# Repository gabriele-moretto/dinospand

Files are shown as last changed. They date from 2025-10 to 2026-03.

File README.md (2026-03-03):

# DinoSpand

The purpose of this board is to be mounted on a fertilizer spreader (an agricultural tool) to manage the drawer in which we load/unload the fertilizer.
While managing the tool, we'll see all the information in the cabin on the little OLED screen on the board, but also we will able to connect the device to our smartphone in order to managing some settings.

## Hardware

The microcontroller used is an ESP32-s3, which is useful for the right number of GPIO we need and for the bluetooth functions.

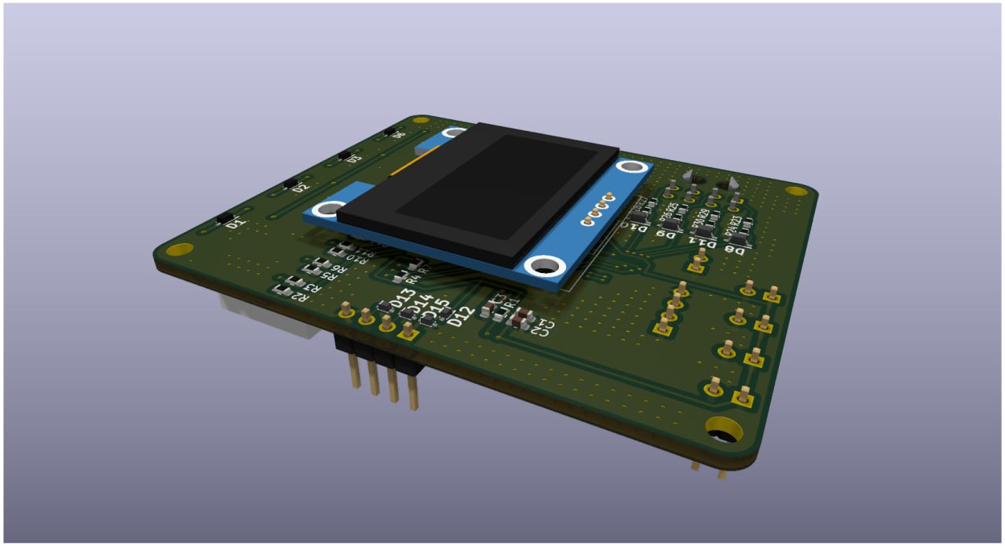
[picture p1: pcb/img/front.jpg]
Front

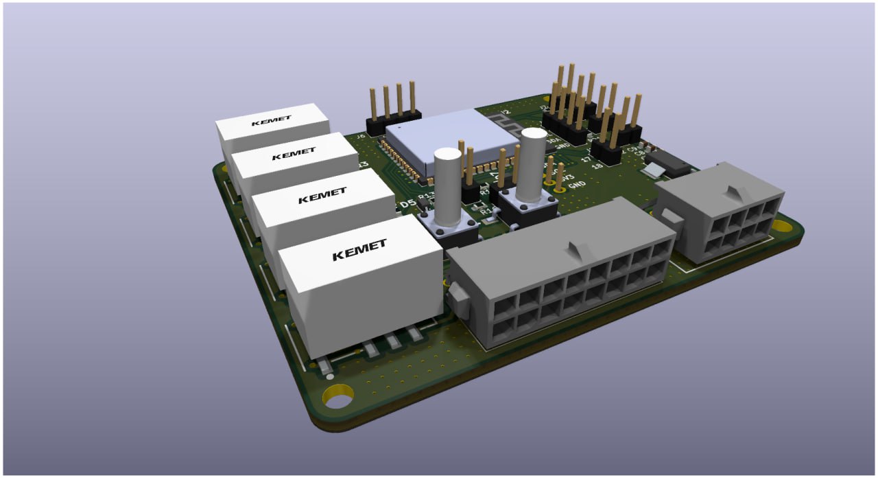
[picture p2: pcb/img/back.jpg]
Back


## Firmware

## [PCBWay](https://www.pcbway.com/) production
I had a great experience working with **PCBWay** through their sponsorship program. They supported my project by manufacturing and shipping a fully assembled PCB, which allowed me to turn my design into a real, working device.

**Key points:**
- PCB manufacturing
- High-quality fabrication and assembly
- Easy ordering process
- Fast production and shipping
- Reliable results

Many thanks to PCBWay for supporting this project!

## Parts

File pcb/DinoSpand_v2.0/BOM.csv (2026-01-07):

Id | Designator | Footprint | Quantity | Designation | Supplier and ref
1 | D7,D5,D4,D11,D8,D10,D9 | SOD2512X110N | 7 | 3.3V
2 | C7,C12,C6,C13,C1 | C_0603_1608Metric | 5 | 10uF
3 | C4,C10,C9 | CP_Radial_D4.0mm_P2.00mm | 3 | xuF
4 | Q2,Q4,Q1,Q3 | SOT96P240X110-3N | 4 | DMN62D0U-7
5 | R21,R16,R22,R8,R19,R20,R18,R12,R1,R6,R11,R29,R4,R15,R3,R25,R7,R27,R23 | R_0603_1608Metric | 19 | 10k
6 | S1,S2 | SW_1571563-6 | 2 | 1571563-6
7 | C8,C11,C5,C14,C15 | C_0603_1608Metric | 5 | xuF
8 | K3,K1,K2,K4 | EE2-5NU | 4 | EE2-5NU
9 | U3,U4 | SOT230P700X180-4N | 2 | LT1963AEST-3.3#TRPBF
10 | J11 | 37946198 | 1 | 3-794619-8
11 | R32,R31 | R_0603_1608Metric | 2 | 100
12 | D16 | LED_0603_1608Metric | 1 | LED
13 | D17 | LED_D3.0mm | 1 | LED
14 | U2 | ESP32S3WROOM1N4 | 1 | ESP32-S3-WROOM-1-N4
15 | R9,R13,R17,R30,R26,R24,R28 | R_0603_1608Metric | 7 | 2.8k
16 | J3 | 47946196 | 1 | 4-794619-6
17 | R10,R14,R2,R5 | R_0603_1608Metric | 4 | 10
18 | D15,D14,D13 | SODFL1608X70N | 3 | SZESD5B5.0ST5G
19 | C2 | C_0603_1608Metric | 1 | 0.1uF
20 | D6,D3,D1,D2 | SODFL2512X90N | 4 | D
21 | C3 | C_0603_1608Metric | 1 | 1uF
22 | D12 | SODFL1608X70N | 1 | D
23 | U1 | 128x64OLED | 1 | Oled64x128

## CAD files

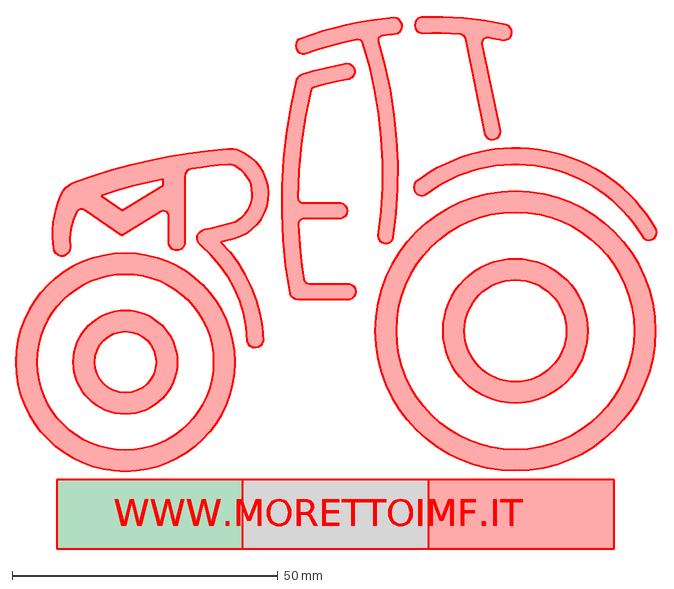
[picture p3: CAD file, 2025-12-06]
logo/logo_MorettoIMF.dxf
WWW.MORETTOIMF.IT

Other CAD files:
logo/Logo Moretto-rev-31-08-2021.dwg

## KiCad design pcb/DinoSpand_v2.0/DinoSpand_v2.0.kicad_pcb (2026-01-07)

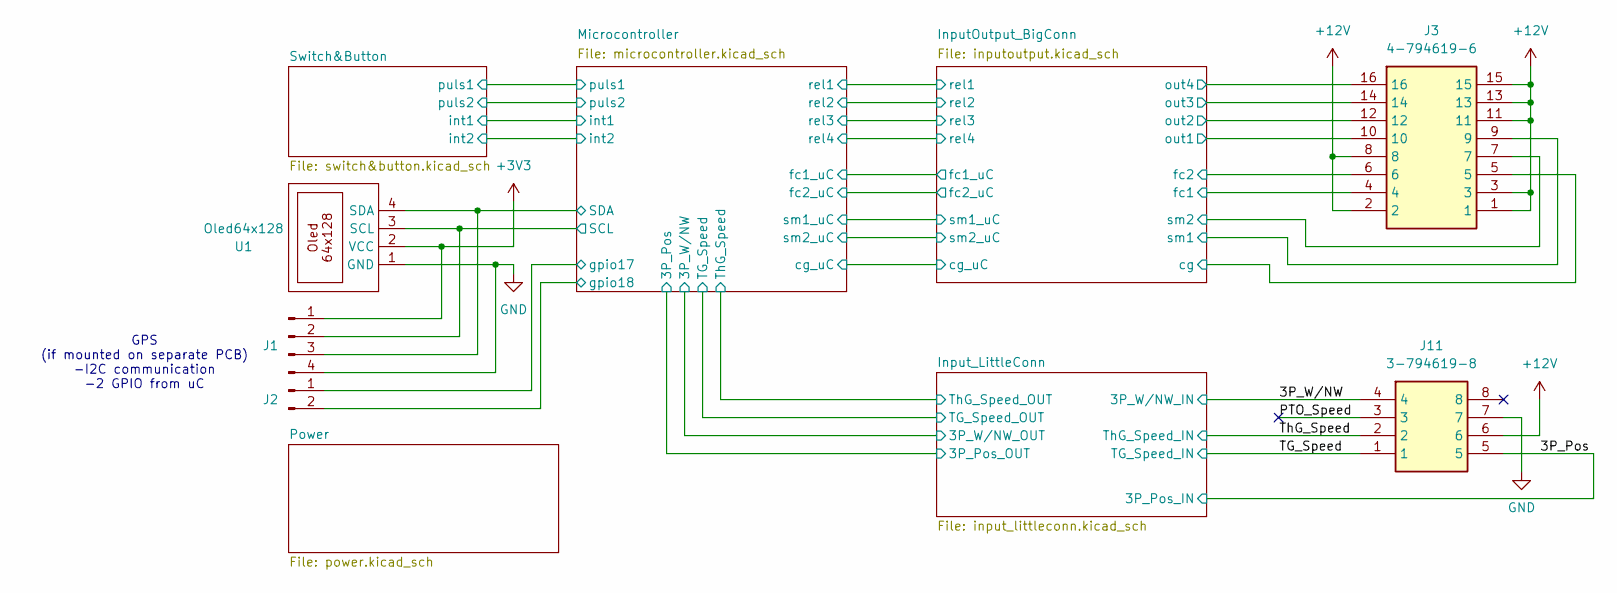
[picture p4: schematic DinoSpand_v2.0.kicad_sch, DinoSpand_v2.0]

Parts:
J1: Conn_01x04_Pin; PinHeader_1x04_P2.54mm_Vertical
J2: Conn_01x02_Pin; PinHeader_1x02_P2.54mm_Vertical
J3: 4-794619-6; 47946196; Mouser Part Number 571-4-794619-6
J11: 3-794619-8; 37946198; Mouser Part Number 571-3-794619-8
U1: Oled64x128; 128x64OLED

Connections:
+3V3: J1.1, U1.2 (VCC); also elsewhere on the board
+12V: J3.1, J3.2, J3.3, J3.8, J3.11, J3.13, J3.15, J11.6; also elsewhere on the board
/3P_Pos: J11.5; also elsewhere on the board
/3P_W/NW: J11.4; also elsewhere on the board
/InputOutput_BigConn/cg: J3.5; also elsewhere on the board
/InputOutput_BigConn/out1: J3.10; also elsewhere on the board
/InputOutput_BigConn/out2: J3.12; also elsewhere on the board
/InputOutput_BigConn/out3: J3.14; also elsewhere on the board
/InputOutput_BigConn/out4: J3.16; also elsewhere on the board
/InputOutput_BigConn/sm1: J3.9; also elsewhere on the board
/InputOutput_BigConn/sm2: J3.7; also elsewhere on the board
/Microcontroller/GPIO10: J3.4; also elsewhere on the board
/Microcontroller/GPIO11: J3.6; also elsewhere on the board
/Microcontroller/GPIO15: J1.3, U1.4 (SDA); also elsewhere on the board
/Microcontroller/GPIO16: J1.2, U1.3 (SCL); also elsewhere on the board
/Microcontroller/GPIO17: J2.1; also elsewhere on the board
/Microcontroller/GPIO18: J2.2; also elsewhere on the board
/PTO_Speed: J11.3
/TG_Speed: J11.1; also elsewhere on the board
/ThG_Speed: J11.2; also elsewhere on the board
GND: J1.4, J11.7, U1.1 (GND); also elsewhere on the board

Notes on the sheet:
GPS (if mounted on separate PCB) -I2C communication -2 GPIO from uC

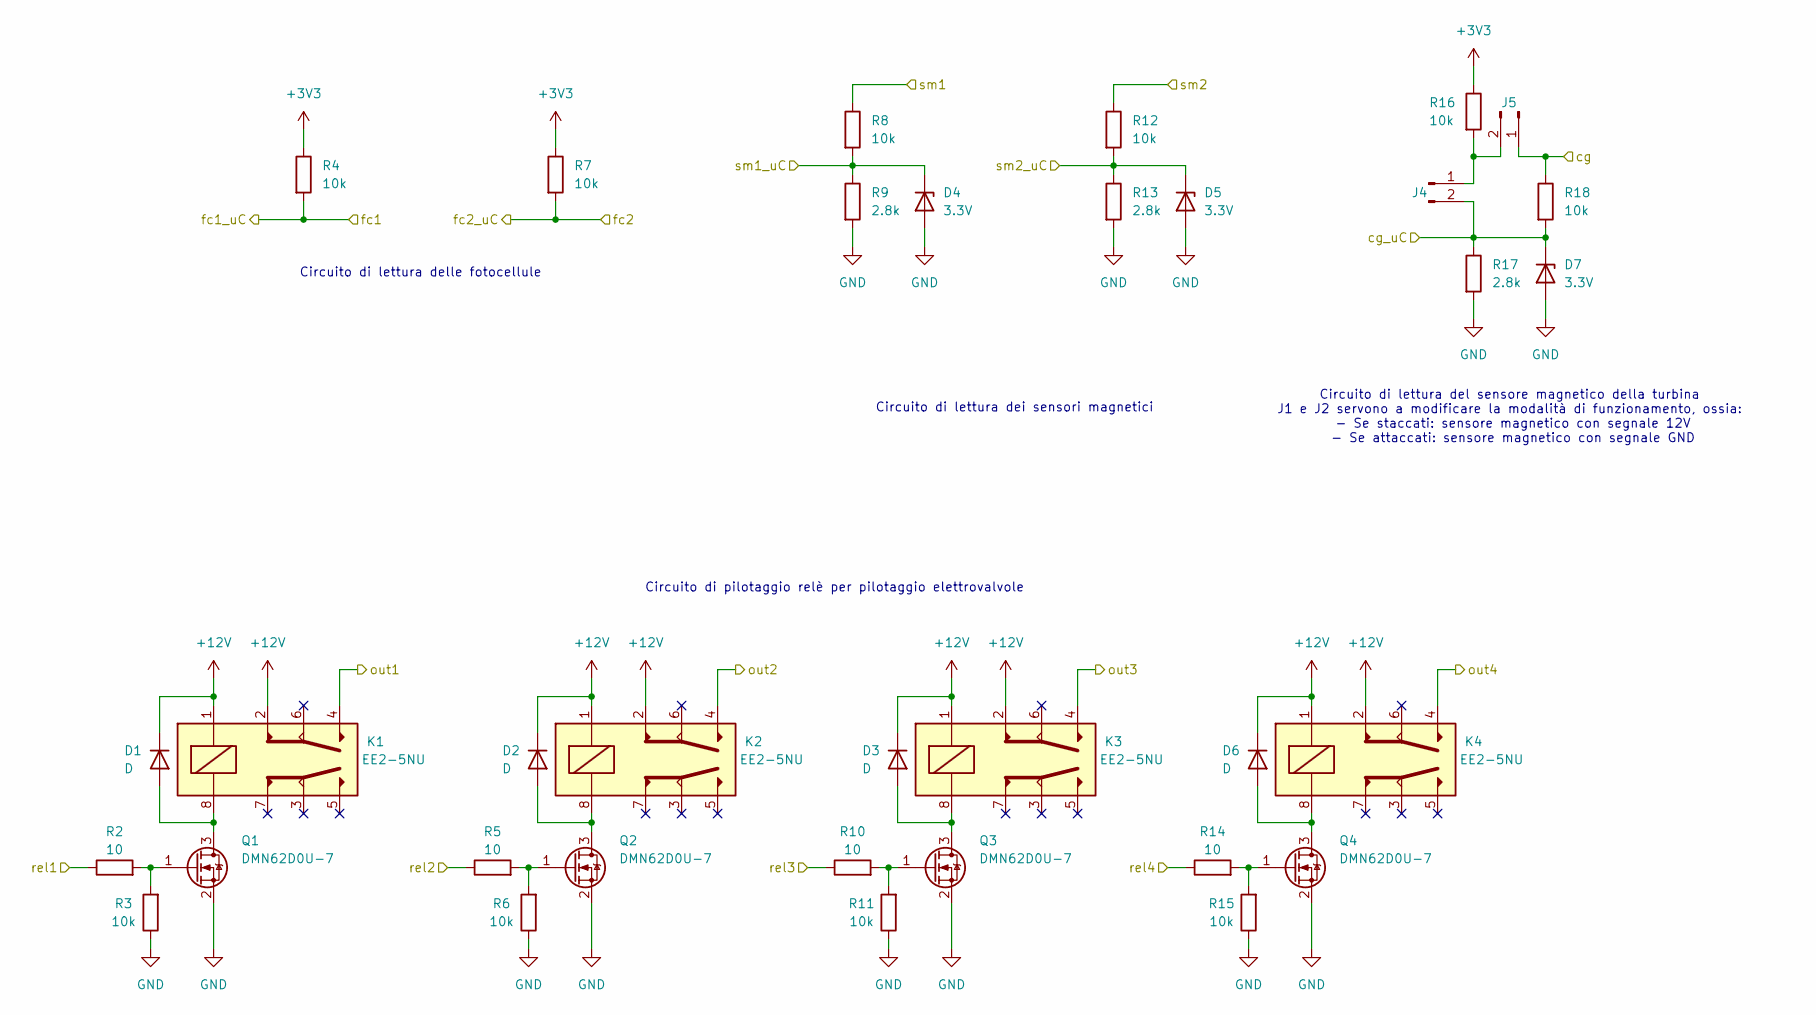
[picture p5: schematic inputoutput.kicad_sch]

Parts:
D1, D2, D3, D6: D; SODFL2512X90N
D4, D5, D7: 3.3V; SOD2512X110N
J4, J5: Conn_01x02_Pin; PinHeader_1x02_P2.54mm_Vertical
K1, K2, K3, K4: EE2-5NU; Mouser Part Number 80-EE2-5NU
Q1, Q2, Q3, Q4: DMN62D0U-7; SOT96P240X110-3N; Mouser Part Number 621-DMN62D0U-7
R2, R5, R10, R14: 10; R_0603_1608Metric
R3, R4, R6, R7, R8, R11, R12, R15, R16, R18: 10k; R_0603_1608Metric
R9, R13, R17: 2.8k; R_0603_1608Metric

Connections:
+3V3: R4.1, R7.1, R16.1; also elsewhere on the board
+12V: D1.1 (K), D2.1 (K), D3.1 (K), D6.1 (K), K1.1, K1.2, K2.1, K2.2, K3.1, K3.2, K4.1, K4.2; also elsewhere on the board
/InputOutput_BigConn/cg: J5.1, R18.1; also elsewhere on the board
/InputOutput_BigConn/out1: K1.4; also elsewhere on the board
/InputOutput_BigConn/out2: K2.4; also elsewhere on the board
/InputOutput_BigConn/out3: K3.4; also elsewhere on the board
/InputOutput_BigConn/out4: K4.4; also elsewhere on the board
/InputOutput_BigConn/sm1: R8.1; also elsewhere on the board
/InputOutput_BigConn/sm2: R12.1; also elsewhere on the board
/Microcontroller/GPIO10: R4.2; also elsewhere on the board
/Microcontroller/GPIO11: R7.2; also elsewhere on the board
/Microcontroller/GPIO12: D4.1 (K), R8.2, R9.1; also elsewhere on the board
/Microcontroller/GPIO13: D5.1 (K), R12.2, R13.1; also elsewhere on the board
/Microcontroller/GPIO14: D7.1 (K), J4.2, R17.1, R18.2; also elsewhere on the board
/Microcontroller/GPIO21: R2.1; also elsewhere on the board
/Microcontroller/GPIO37: R14.1; also elsewhere on the board
/Microcontroller/GPIO47: R5.1; also elsewhere on the board
/Microcontroller/GPIO48: R10.1; also elsewhere on the board
GND: D4.2 (A), D5.2 (A), D7.2 (A), Q1.2 (S), Q2.2 (S), Q3.2 (S), Q4.2 (S), R3.1, R6.1, R9.2, R11.1, R13.2, R15.1, R17.2; also elsewhere on the board
unnamed: D1.2 (A), K1.8, Q1.3 (D)
unnamed: D2.2 (A), K2.8, Q2.3 (D)
unnamed: D3.2 (A), K3.8, Q3.3 (D)
unnamed: D6.2 (A), K4.8, Q4.3 (D)
unnamed: J4.1, J5.2, R16.2
unnamed: Q1.1 (G), R2.2, R3.2
unnamed: Q2.1 (G), R5.2, R6.2
unnamed: Q3.1 (G), R10.2, R11.2
unnamed: Q4.1 (G), R14.2, R15.2

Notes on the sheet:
Circuito di pilotaggio relè per pilotaggio elettrovalvole
Circuito di lettura del sensore magnetico della turbina J1 e J2 servono a modificare la modalità di funzionamento, ossia: - Se staccati: sensore magnetico con segnale 12V - Se attaccati: sensore magnetico con segnale GND
Circuito di lettura dei sensori magnetici
Circuito di lettura delle fotocellule

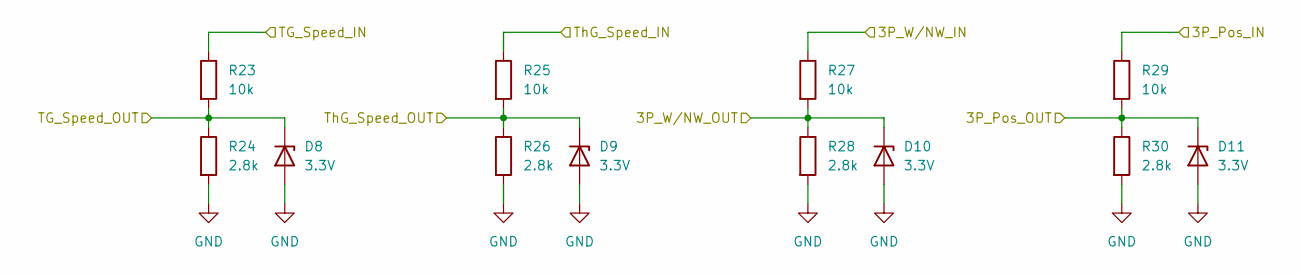
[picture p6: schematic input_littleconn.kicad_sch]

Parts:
D8, D9, D10, D11: 3.3V; SOD2512X110N
R23, R25, R27, R29: 10k; R_0603_1608Metric
R24, R26, R28, R30: 2.8k; R_0603_1608Metric

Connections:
/3P_Pos: R29.1; also elsewhere on the board
/3P_W/NW: R27.1; also elsewhere on the board
/Microcontroller/GPIO9: D10.1 (K), R27.2, R28.1; also elsewhere on the board
/Microcontroller/GPIO35: D9.1 (K), R25.2, R26.1; also elsewhere on the board
/Microcontroller/GPIO36: D8.1 (K), R23.2, R24.1; also elsewhere on the board
/Microcontroller/GPIO38: D11.1 (K), R29.2, R30.1; also elsewhere on the board
/TG_Speed: R23.1; also elsewhere on the board
/ThG_Speed: R25.1; also elsewhere on the board
GND: D8.2 (A), D9.2 (A), D10.2 (A), D11.2 (A), R24.2, R26.2, R28.2, R30.2; also elsewhere on the board

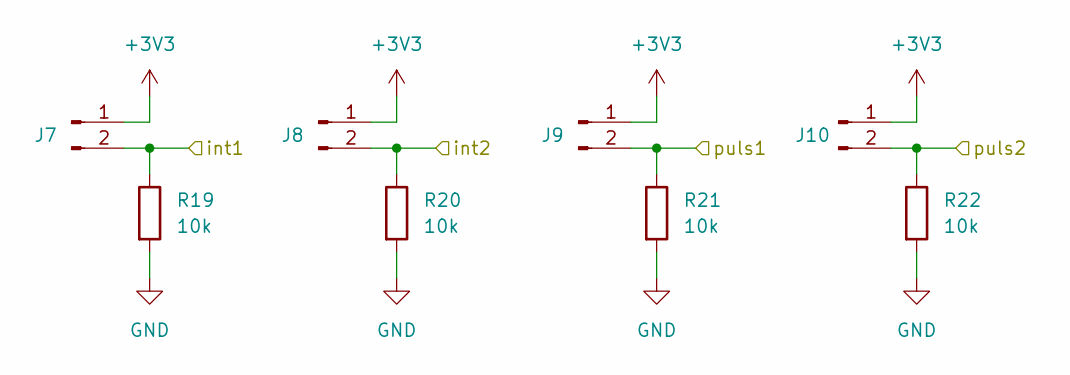
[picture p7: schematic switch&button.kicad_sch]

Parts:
J7, J8, J9, J10: Conn_01x02_Pin; PinHeader_1x02_P2.54mm_Vertical
R19, R20, R21, R22: 10k; R_0603_1608Metric

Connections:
+3V3: J7.1, J8.1, J9.1, J10.1; also elsewhere on the board
/Microcontroller/GPIO4: J7.2, R19.1; also elsewhere on the board
/Microcontroller/GPIO5: J8.2, R20.1; also elsewhere on the board
/Microcontroller/GPIO6: J9.2, R21.1; also elsewhere on the board
/Microcontroller/GPIO7: J10.2, R22.1; also elsewhere on the board
GND: R19.2, R20.2, R21.2, R22.2; also elsewhere on the board

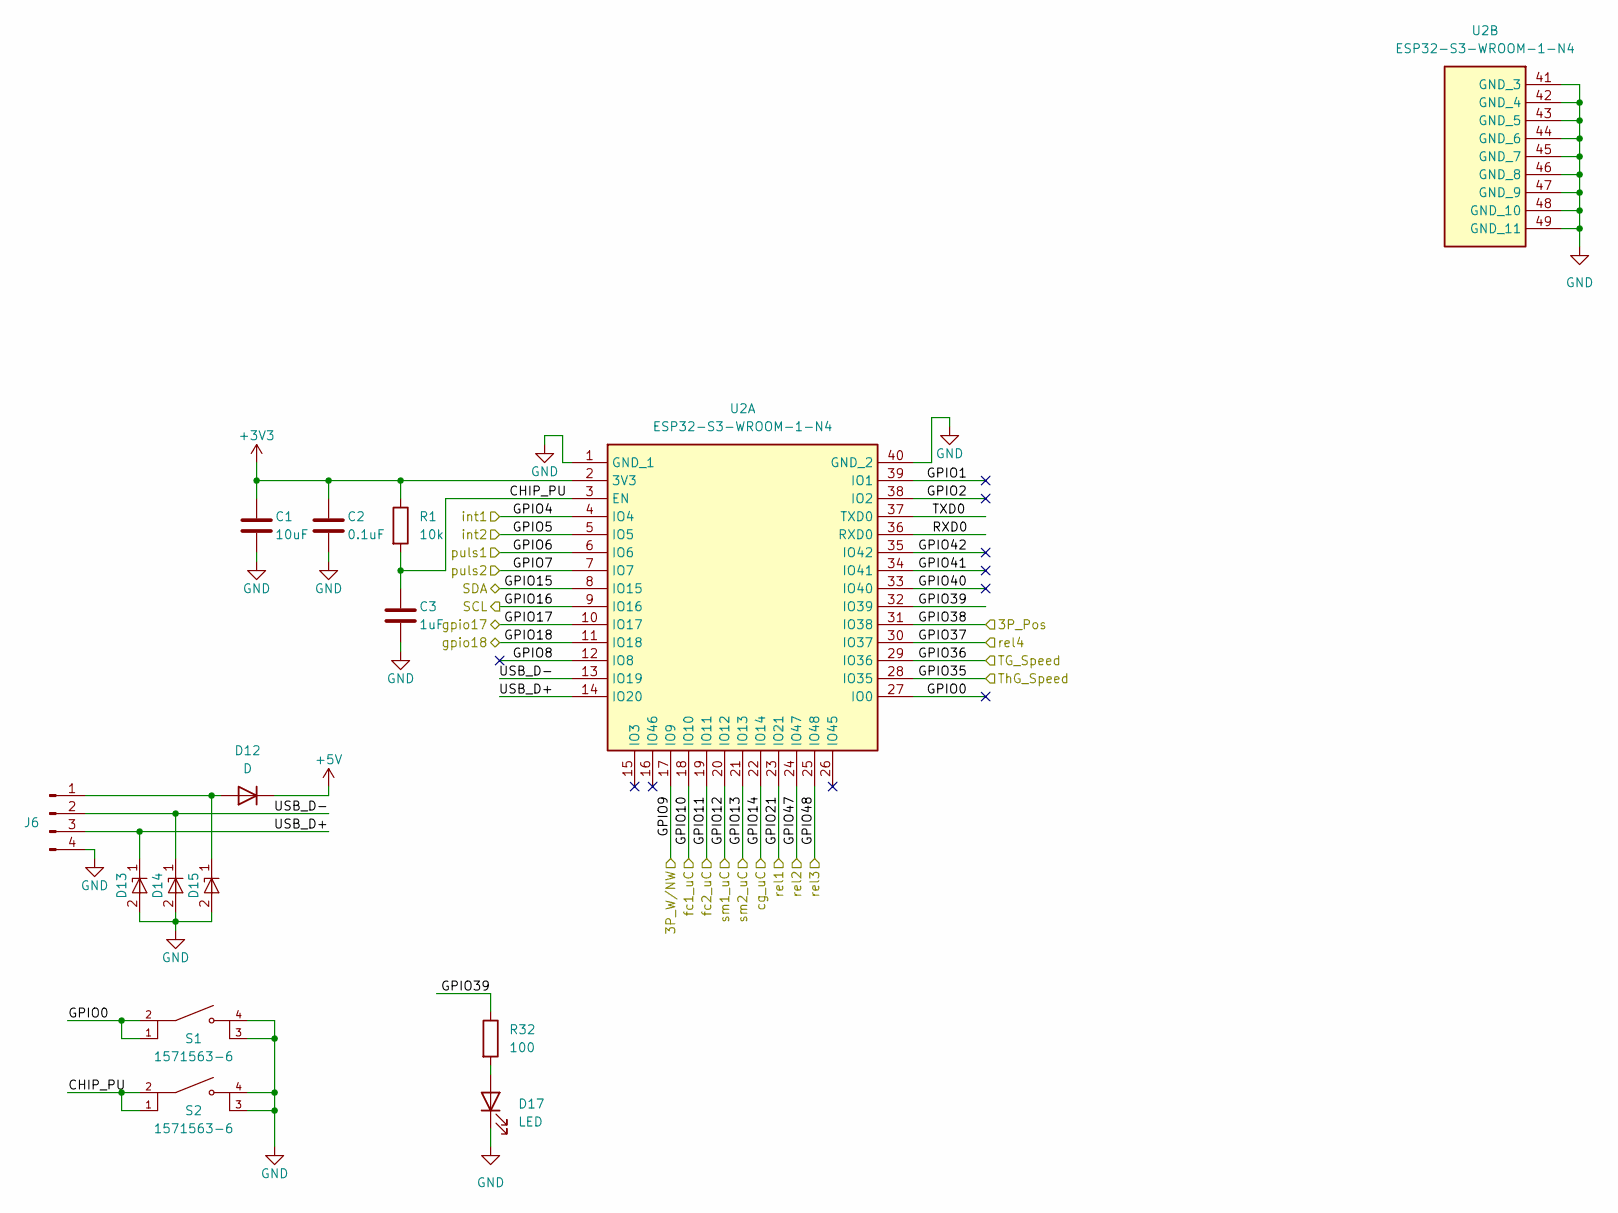
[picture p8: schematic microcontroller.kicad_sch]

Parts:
C1: 10uF; C_0603_1608Metric
C2: 0.1uF; C_0603_1608Metric
C3: 1uF; C_0603_1608Metric
D12: D; SODFL1608X70N
D13, D14, D15: SZESD5B5.0ST5G; SODFL1608X70N; Mouser Part Number 863-SZESD5B5.0ST5G
D17: LED; LED_D3.0mm
J6: Conn_01x04_Pin; PinHeader_1x04_P2.54mm_Vertical
R1: 10k; R_0603_1608Metric
R32: 100; R_0603_1608Metric
S1, S2: 1571563-6; SW_1571563-6; PARTREV V
U2: ESP32-S3-WROOM-1-N4; ESP32S3WROOM1N4; Mouser Part Number 356-ESP32-S3WROOM1N4

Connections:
+3V3: C1.1, C2.1, R1.1, U2.2 (3V3); also elsewhere on the board
+5V: D12.1 (K); also elsewhere on the board
/Microcontroller/CHIP_PU: C3.1, R1.2, S2.1, S2.2, U2.3 (EN)
/Microcontroller/GPIO0: S1.1, S1.2, U2.27 (IO0)
/Microcontroller/GPIO1: U2.39 (IO1)
/Microcontroller/GPIO2: U2.38 (IO2)
/Microcontroller/GPIO4: U2.4 (IO4); also elsewhere on the board
/Microcontroller/GPIO5: U2.5 (IO5); also elsewhere on the board
/Microcontroller/GPIO6: U2.6 (IO6); also elsewhere on the board
/Microcontroller/GPIO7: U2.7 (IO7); also elsewhere on the board
/Microcontroller/GPIO8: U2.12 (IO8)
/Microcontroller/GPIO9: U2.17 (IO9); also elsewhere on the board
/Microcontroller/GPIO10: U2.18 (IO10); also elsewhere on the board
/Microcontroller/GPIO11: U2.19 (IO11); also elsewhere on the board
/Microcontroller/GPIO12: U2.20 (IO12); also elsewhere on the board
/Microcontroller/GPIO13: U2.21 (IO13); also elsewhere on the board
/Microcontroller/GPIO14: U2.22 (IO14); also elsewhere on the board
/Microcontroller/GPIO15: U2.8 (IO15); also elsewhere on the board
/Microcontroller/GPIO16: U2.9 (IO16); also elsewhere on the board
/Microcontroller/GPIO17: U2.10 (IO17); also elsewhere on the board
/Microcontroller/GPIO18: U2.11 (IO18); also elsewhere on the board
/Microcontroller/GPIO21: U2.23 (IO21); also elsewhere on the board
/Microcontroller/GPIO35: U2.28 (IO35); also elsewhere on the board
/Microcontroller/GPIO36: U2.29 (IO36); also elsewhere on the board
/Microcontroller/GPIO37: U2.30 (IO37); also elsewhere on the board
/Microcontroller/GPIO38: U2.31 (IO38); also elsewhere on the board
/Microcontroller/GPIO39: R32.1, U2.32 (IO39)
/Microcontroller/GPIO40: U2.33 (IO40)
/Microcontroller/GPIO41: U2.34 (IO41)
/Microcontroller/GPIO42: U2.35 (IO42)
/Microcontroller/GPIO47: U2.24 (IO47); also elsewhere on the board
/Microcontroller/GPIO48: U2.25 (IO48); also elsewhere on the board
/Microcontroller/RXD0: U2.36 (RXD0)
/Microcontroller/TXD0: U2.37 (TXD0)
/Microcontroller/USB_D+: D13.1 (K1), J6.3, U2.14 (IO20)
/Microcontroller/USB_D-: D14.1 (K1), J6.2, U2.13 (IO19)
GND: C1.2, C2.2, C3.2, D13.2 (A), D14.2 (A), D15.2 (A), D17.1 (K), J6.4, S1.3, S1.4, S2.3, S2.4, U2.1 (GND_1), U2.40 (GND_2), U2.41 (GND_3), U2.42 (GND_4), U2.43 (GND_5), U2.44 (GND_6), U2.45 (GND_7), U2.46 (GND_8), U2.47 (GND_9), U2.48 (GND_10), U2.49 (GND_11); also elsewhere on the board
unnamed: D12.2 (A), D15.1 (K1), J6.1
unnamed: D17.2 (A), R32.2

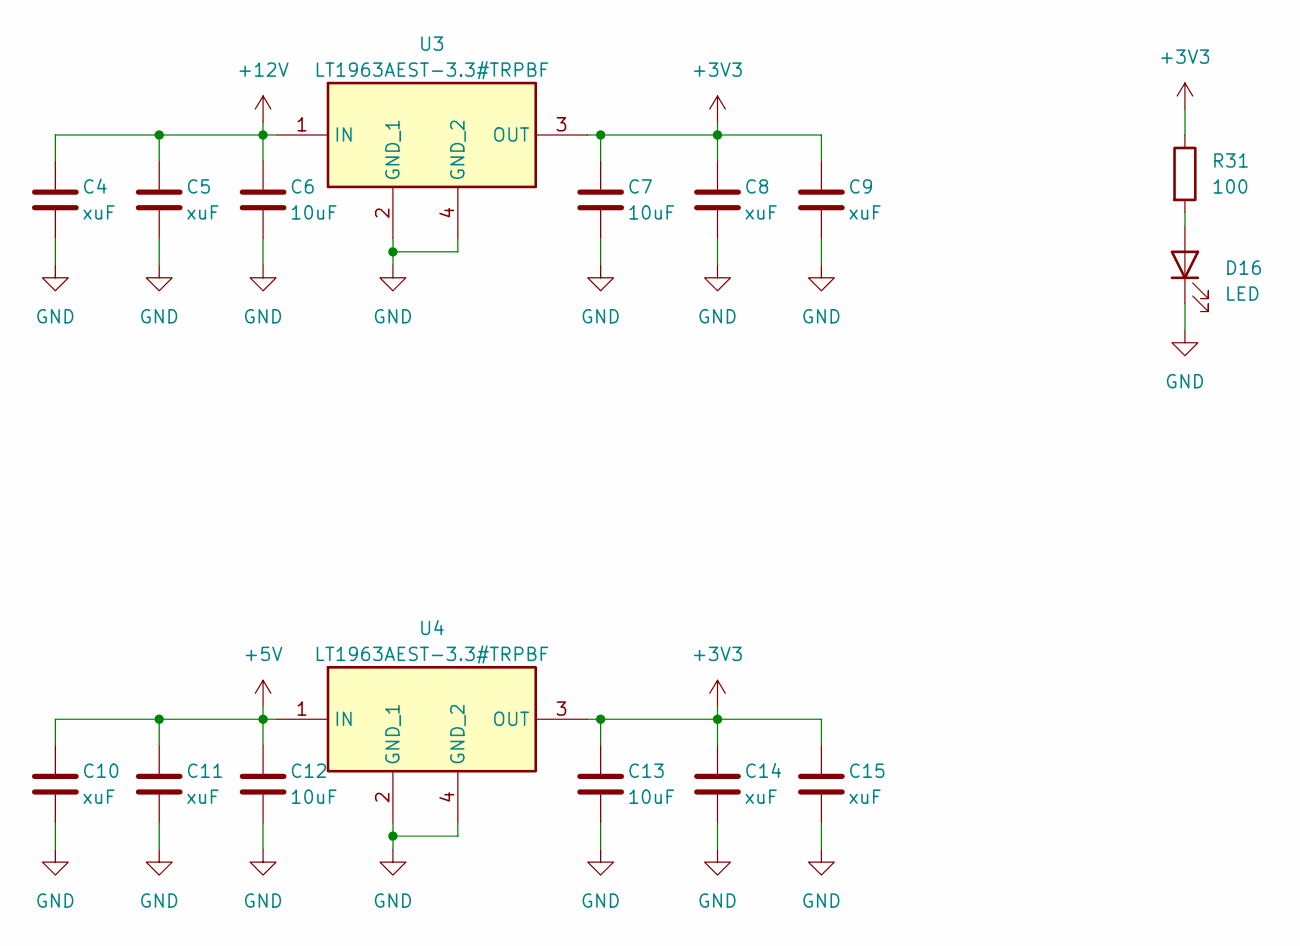
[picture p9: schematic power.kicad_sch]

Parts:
C4, C9, C10: xuF; CP_Radial_D4.0mm_P2.00mm
C5, C8, C11, C14, C15: xuF; C_0603_1608Metric
C6, C7, C12, C13: 10uF; C_0603_1608Metric
D16: LED; LED_0603_1608Metric
R31: 100; R_0603_1608Metric
U3, U4: LT1963AEST-3.3#TRPBF; SOT230P700X180-4N; Mouser Part Number 584-1963AEST-3.3TPF

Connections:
+3V3: C7.1, C8.1, C9.1, C13.1, C14.1, C15.1, R31.1, U3.3 (OUT), U4.3 (OUT); also elsewhere on the board
+5V: C10.1, C11.1, C12.1, U4.1 (IN); also elsewhere on the board
+12V: C4.1, C5.1, C6.1, U3.1 (IN); also elsewhere on the board
GND: C4.2, C5.2, C6.2, C7.2, C8.2, C9.2, C10.2, C11.2, C12.2, C13.2, C14.2, C15.2, D16.1 (K), U3.2 (GND_1), U3.4 (GND_2), U4.2 (GND_1), U4.4 (GND_2); also elsewhere on the board
unnamed: D16.2 (A), R31.2

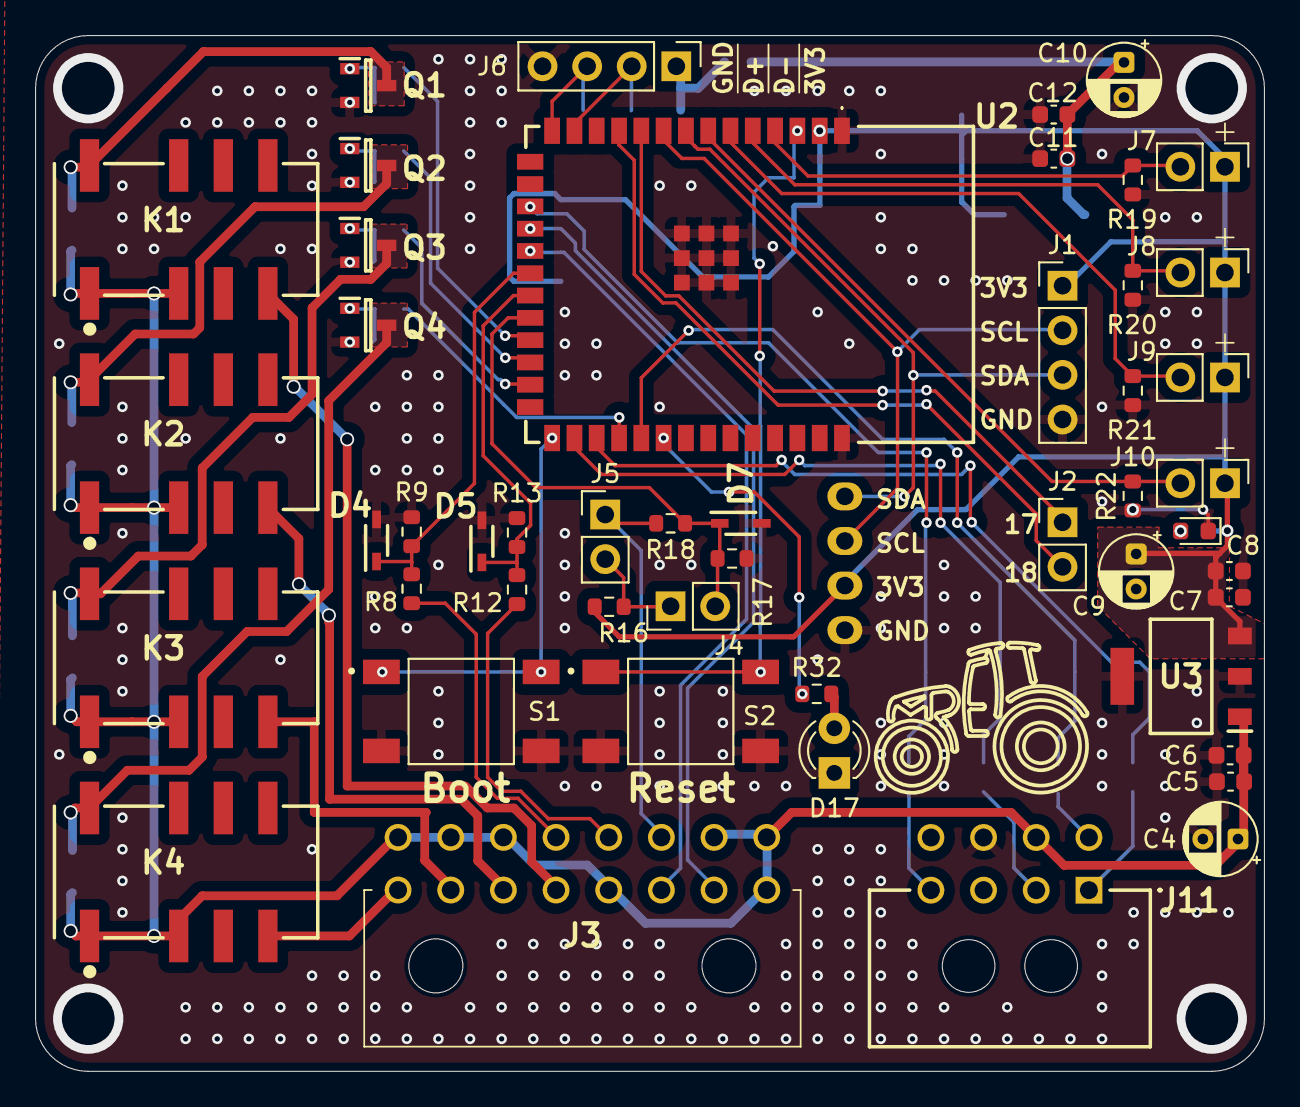
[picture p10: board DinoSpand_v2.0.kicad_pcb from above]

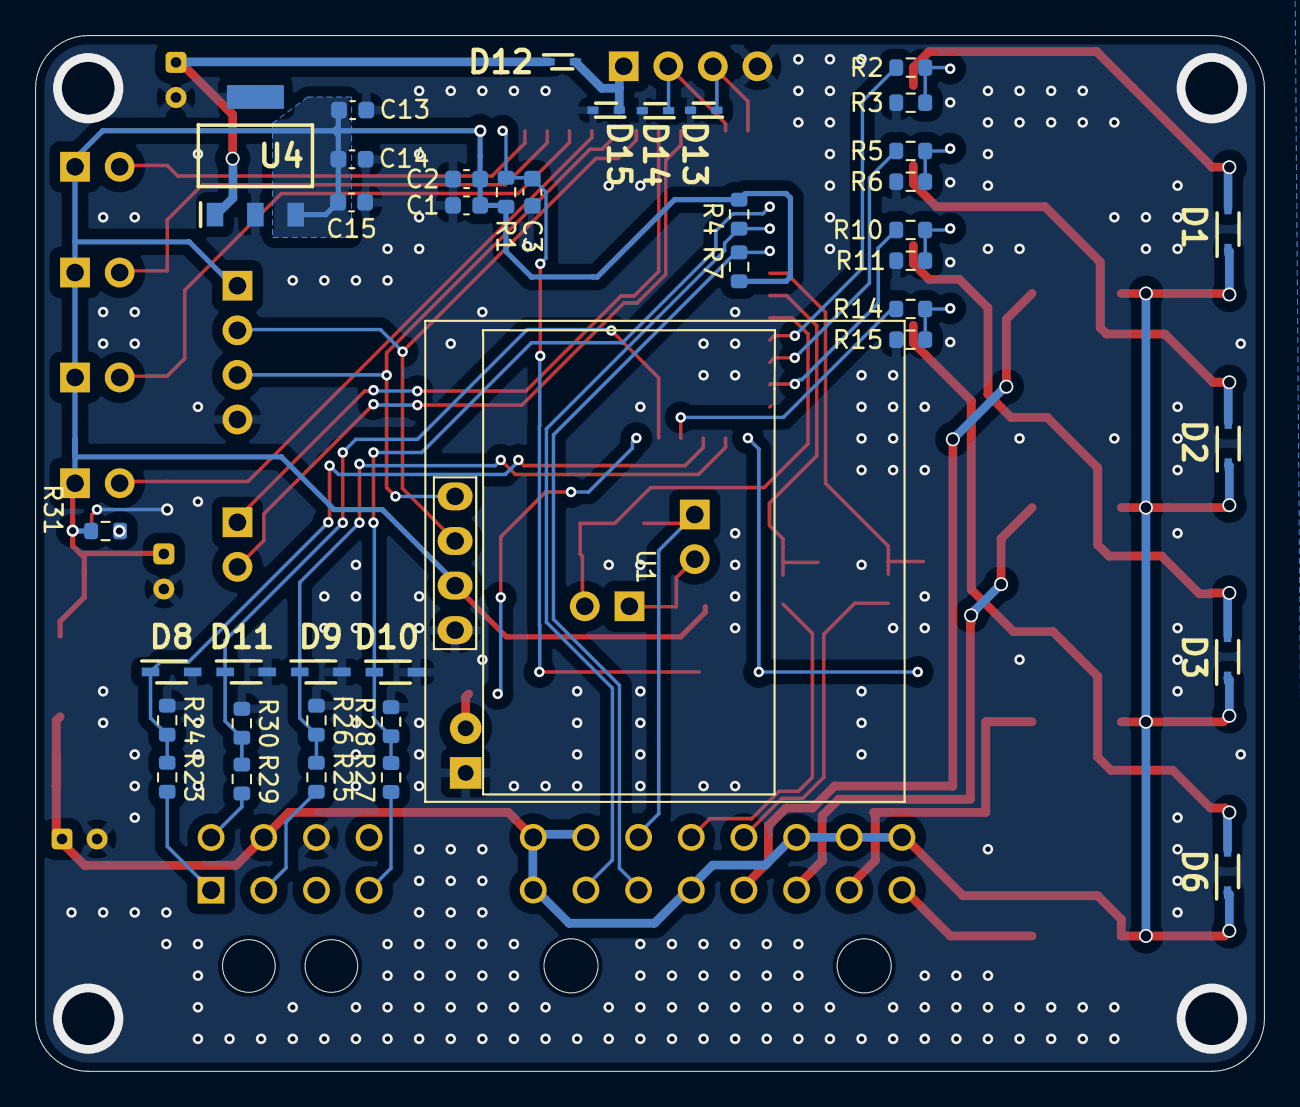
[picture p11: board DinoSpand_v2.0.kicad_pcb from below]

Board: 2 copper layers, 70.0 x 59.0 mm, 89 parts (40 on the bottom side), 53 nets.

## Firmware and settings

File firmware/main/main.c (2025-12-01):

#include <stdio.h>
#include "string.h"
#include "freertos/FreeRTOS.h"
#include "freertos/task.h"
#include "esp_intr_alloc.h"
#include "driver/gpio.h"
#include "driver/i2c_master.h"
#include "gpio.h"
#include "frequency.h"
#include "esp_timer.h"
#include "ssd1306.h"
#include "screen.h"
#include "states.h"
#include "bitmap_img.h"

//Debug mode
#define DEBUG

//General state
static uint8_t sys_state;

//Struct unica che contiene tutte le informazioni di un oggetto
typedef struct{
    drawer_in *inputs;
    drawer_out *outputs;
    uint8_t state;
}drawer_t;

drawer_t drawer_sx = {
    .inputs = &drawer_sx_in,
    .outputs = &drawer_sx_out,
    .state = 0
};

drawer_t drawer_dx = {
    .inputs = &drawer_dx_in,
    .outputs = &drawer_dx_out,
    .state = 0
};

//Tempistiche
int delayAfterDetect; //ms
int dischargeTime; //ms
int chargeTime; //ms
int closeTime; //ms

//Gestore dei relè
void drawer_output_handler(void *pvParameters){
    drawer_t *drawer = (drawer_t*) pvParameters;
    //char task_name[configMAX_TASK_NAME_LEN] = pcTaskGetName(NULL);

    while(1){
        TickType_t last_wake_time = xTaskGetTickCount();

        switch (sys_state) {
        case INIT:
            gpio_set_level(drawer->outputs->drawer_down, 1);
            gpio_set_level(drawer->outputs->drawer_up, 1);
            break;

        case WORK:
            switch (drawer->state) {
            case WAIT:
                if(drawer->inputs->start_state || drawer->inputs->tail)
                    drawer->state++;
                break;
            
            case DELAY:
                vTaskDelayUntil(&last_wake_time, pdMS_TO_TICKS(delayAfterDetect));
                gpio_set_level(drawer->outputs->drawer_down, 0);
                drawer->state++;
                break;

            case DISCHARGE:
                vTaskDelayUntil(&last_wake_time, pdMS_TO_TICKS(dischargeTime));
                gpio_set_level(drawer->outputs->drawer_down, 1);

                if(drawer->inputs->read_mag_sens) {
                    if(gpio_get_level(drawer->inputs->mag_sens))
                        drawer->state++;
                } else {
                    vTaskDelayUntil(&last_wake_time, pdMS_TO_TICKS(closeTime));
                    gpio_set_level(drawer->outputs->drawer_up, 0);
                    drawer->state++;
                }
                break;

            case CHARGE:
                vTaskDelayUntil(&last_wake_time, pdMS_TO_TICKS(chargeTime));
                gpio_set_level(drawer->outputs->drawer_up, 1);

                vTaskDelayUntil(&last_wake_time, pdMS_TO_TICKS(closeTime));
                gpio_set_level(drawer->outputs->drawer_up, 0);

                drawer->state = WAIT;
                break;
            
            default:
                gpio_set_level(drawer->outputs->drawer_down, 1);
                gpio_set_level(drawer->outputs->drawer_up, 1);
                break;
            }
            break;

        case ERROR:
            gpio_set_level(drawer->outputs->drawer_down, 1);
            gpio_set_level(drawer->outputs->drawer_up, 1);
            break;
        
        default:
            gpio_set_level(drawer->outputs->drawer_down, 1);
            gpio_set_level(drawer->outputs->drawer_up, 1);
            break;
        }

        if((drawer->state =! DELAY) && (drawer->inputs->start_state))
            drawer->inputs->tail = true;

        vTaskDelay(10 / portTICK_PERIOD_MS);
    }
}

//Gestione della lettura degli input relativi ai cassetti
void drawer_inputs_handler(void *pvParameters) {
    drawer_in *input = (drawer_in*) pvParameters;

    while(1){
        bool poplar = gpio_get_level(input->photocell) && gpio_get_level(input->int_fot);
        bool manual = gpio_get_level(input->puls);

        if(poplar || manual)
            input->start_state = true;
        else
            input->start_state = false;

        vTaskDelay(10 / portTICK_PERIOD_MS);
    }
}

//Costanti per info prese dalla cabina
#define FREQ_AT_1KMH 2.166
#define FREQ_AT_2RPS 12.0

//Strutture dati delle info prese dalla cabina
input_freq pto_pos = {
    .gpio = PTO_POS_GPIO,
    .measuring = false
};

input_freq thg_speed = {
    .gpio = THG_SPEED_GPIO,
    .measuring = false
};

input_freq tg_speed = {
    .gpio = TG_SPEED_GPIO,
    .measuring = false
};

bool pto_work;

//Costanti per i servizi di interrupt
#define ISR_ON_TIME 500     //ms
#define ISR_OFF_TIME 5000   //ms

//Variabili dei valori letti dal connettore in cabina
double tg_speed_val, thg_speed_val, pto_pos_val;

//Gestione degli input del connettore in cabina
void tractor_input_handler(void *pvParameters) {
    bool enable = true;
    int64_t start_t;

    start_t = esp_timer_get_time();

    while(1) {
        tg_speed_val = tg_speed.frequency / FREQ_AT_1KMH; // km/h
        thg_speed_val = thg_speed.frequency / FREQ_AT_1KMH; // km/h
        pto_pos_val = pto_pos.frequency / FREQ_AT_2RPS; // rps

        if(gpio_get_level(PTO_WORK_GPIO) == 1)
            pto_work = true;
        else
            pto_work = false;

        //Abilito l'ISR per ISR_ON_TIME ms e disabilito per ISR_OFF_TIME ms
        if(enable && (esp_timer_get_time() - start_t) > ISR_ON_TIME) {
            gpio_set_intr_type(PTO_POS_GPIO, GPIO_INTR_DISABLE);
            gpio_set_intr_type(THG_SPEED_GPIO, GPIO_INTR_DISABLE);
            gpio_set_intr_type(TG_SPEED_GPIO, GPIO_INTR_DISABLE);
            
            enable = false;
            start_t = esp_timer_get_time();
        } else if(!enable && (esp_timer_get_time() - start_t) > ISR_OFF_TIME) {
            gpio_set_intr_type(PTO_POS_GPIO, GPIO_INTR_ANYEDGE);
            gpio_set_intr_type(THG_SPEED_GPIO, GPIO_INTR_ANYEDGE);
            gpio_set_intr_type(TG_SPEED_GPIO, GPIO_INTR_ANYEDGE);
            
            enable = true;
            start_t = esp_timer_get_time();
        }

        vTaskDelay(10 / portTICK_PERIOD_MS);
    }
}

//Variabili degli schermi oled
#define SC1_ADDR 0x3D
#define SC2_ADDR 0x3C

#define I2C_MASTER_FREQ 400000

SSD1306_t screen1, screen2;

int8_t x_pos_side (uint8_t side, uint8_t x_offset, uint8_t width) {
    if(side == SX_SIDE)
        return x_offset;
    else if(side == DX_SIDE)
        return (128 - x_offset - width);
    else
        return 0;
}

void show_drawer_info(SSD1306_t * screen, uint8_t state, uint8_t side) {
    uint8_t x_pos = 0, y_pos = 0;
    int8_t sign = 0;

    if(side == SX_SIDE) 
        x_pos = SX_X_POS;
    else if(side == DX_SIDE)
        x_pos = DX_X_POS;

    if(side == SX_SIDE) 
        y_pos = SX_Y_POS;
    else if(side == DX_SIDE)
        y_pos = DX_Y_POS;
    

    switch (state)
    {
    case WAIT:
        ssd1306_bitmaps(
                screen,
                x_pos, 
                y_pos, 
                drawer_empty.array, 
                drawer_empty.width, 
                drawer_empty.height, 
                false);
            
        ssd1306_bitmaps(
                screen,
                x_pos_side(side, 4 + drawer_empty.width, automatic.width), 
                y_pos, 
                automatic.array, 
                automatic.width, 
                automatic.height, 
                false);
        
        ssd1306_bitmaps(
                screen,
                x_pos_side(side, 4 + drawer_empty.width, photocell_on.width), 
                y_pos + 32, 
                photocell_on.array, 
                photocell_on.width, 
                photocell_on.height, 
                false);
        break;
    
    case DELAY:
        
        break;

    case CHARGE:
        
        break;

    case DISCHARGE:
        
        break;
    
    default:
        break;
    }
}

void manage_screens(void *pvParameters) {
    ssd1306_clear_screen(&screen1, false);
    ssd1306_clear_screen(&screen2, false);

	ssd1306_contrast(&screen1, 0xff);
    ssd1306_contrast(&screen2, 0xff);

    while(1) {
        switch (sys_state)
        {
        case INIT:
            ssd1306_bitmaps(
                &screen1,
                screen1._width/2 - morettoimf_big.width/2, 
                0, 
                morettoimf_big.array, 
                morettoimf_big.width, 
                morettoimf_big.height, 
                false);
            ssd1306_display_text_box1(&screen1, 6, 24, "MorettoIMF", 10, 10, false, 100);

            ssd1306_display_text_box1(&screen2, 3, 30, "DinoSpand", 9, 9, false, 100);
            ssd1306_display_text_box1(&screen2, 4, 48, "v2.0", 4, 4, false, 100);
            ssd1306_display_text_box1(&screen2, 5, 24, "MorettoIMF", 10, 10, false, 100);

            vTaskDelay(1000 / portTICK_PERIOD_MS);
            ssd1306_clear_screen(&screen1, false);
            ssd1306_clear_screen(&screen2, false);
            sys_state = WORK;
            break;
        
        case WORK:
            show_drawer_info(&screen1, drawer_sx.state, SX_SIDE);
            show_drawer_info(&screen2, drawer_dx.state, DX_SIDE);
            break;
        
        case ERROR:
            ssd1306_display_text_x3(&screen1, 0, "ERROR", 5, false);
            ssd1306_display_text_x3(&screen2, 0, "ERROR", 5, false);
            break;
        
        default:
            break;
        }

        vTaskDelay(100 / portTICK_PERIOD_MS);
    }
}

//Inizializza le variabili e carica gli elementi salvati in memoria
void var_init(void) {
    sys_state = INIT;

    drawer_sx.state = 0;
    drawer_sx.inputs->start_state = false;
    drawer_sx.inputs->tail = false;

    drawer_dx.state = 0;
    drawer_sx.inputs->start_state = false;
    drawer_sx.inputs->tail = false;

    #if CONFIG_I2C_PORT_0
        i2c_port_t i2c_num = I2C_NUM_0;
    #else
        i2c_port_t i2c_num = I2C_NUM_1;
    #endif

    i2c_master_bus_config_t i2c_mst_config = {
		.clk_source = I2C_CLK_SRC_DEFAULT,
		.glitch_ignore_cnt = 7,
		.i2c_port = i2c_num,
		.scl_io_num = CONFIG_SCL_GPIO,
		.sda_io_num = CONFIG_SDA_GPIO,
		.flags.enable_internal_pullup = true,
	};
	i2c_master_bus_handle_t bus_handle;
    ESP_ERROR_CHECK(i2c_new_master_bus(&i2c_mst_config, &bus_handle));

	screen1._i2c_bus_handle = bus_handle;
	i2c_device_add(&screen1, i2c_num, CONFIG_RESET_GPIO, SC1_ADDR);

	screen2._i2c_bus_handle = bus_handle;
    i2c_device_add(&screen2, i2c_num, CONFIG_RESET_GPIO, SC2_ADDR);

    ssd1306_init(&screen1, 128, 64);
    ssd1306_init(&screen2, 128, 64);

    delayAfterDetect = 1000;
    dischargeTime = 500;
    chargeTime = 500;
    closeTime = 50;
}

void io_init(void) {
    // ---- OUTPUT ----
    gpio_config_t io_conf_out = {
        .mode = GPIO_MODE_OUTPUT,
        .pin_bit_mask =
            (1ULL << drawer_sx_out.drawer_up)   |
            (1ULL << drawer_sx_out.drawer_down) |
            (1ULL << drawer_dx_out.drawer_up)   |
            (1ULL << drawer_dx_out.drawer_down),
        .intr_type = GPIO_INTR_DISABLE,
        .pull_down_en = GPIO_PULLDOWN_DISABLE,
        .pull_up_en = GPIO_PULLUP_DISABLE
    };
    gpio_config(&io_conf_out);

    // ---- INPUT ----
    gpio_config_t io_conf_in = {
        .mode = GPIO_MODE_INPUT,
        .pin_bit_mask =
            (1ULL << drawer_sx_in.photocell)    |
            (1ULL << drawer_sx_in.int_fot)      |
            (1ULL << drawer_sx_in.puls)         |
            (1ULL << drawer_dx_in.photocell)    |
            (1ULL << drawer_dx_in.int_fot)      |
            (1ULL << drawer_dx_in.puls)         |
            (1ULL << PTO_WORK_GPIO),
        .intr_type = GPIO_INTR_DISABLE,
        .pull_down_en = GPIO_PULLDOWN_DISABLE,
        .pull_up_en = GPIO_PULLUP_DISABLE
    };

    gpio_config(&io_conf_in);

    gpio_config_t io_conf_int = {
        .mode = GPIO_MODE_INPUT,
        .pin_bit_mask = 
            (1ULL << PTO_POS_GPIO)              |
            (1ULL << THG_SPEED_GPIO)            |
            (1ULL << TG_SPEED_GPIO),
        .intr_type = GPIO_INTR_ANYEDGE,
        .pull_down_en = GPIO_PULLDOWN_DISABLE,
        .pull_up_en = GPIO_PULLUP_DISABLE
    };

    gpio_config(&io_conf_int);

    gpio_install_isr_service(0);
    gpio_isr_handler_add(PTO_POS_GPIO, measure_frequency, (void*) &pto_pos);
    gpio_isr_handler_add(THG_SPEED_GPIO, measure_frequency, (void*) &thg_speed);
    gpio_isr_handler_add(TG_SPEED_GPIO, measure_frequency, (void*) &tg_speed);
}

void print_drawer(drawer_t drawer){
    print_drawer_input(*(drawer.inputs));
    print_drawer_output(*(drawer.outputs));

    switch (drawer.state)
    {
    case WAIT:
        printf("Stato: stop\n");
        break;
    
    case DELAY:
        printf("Stato: tempo di attesa per inizio ciclo\n");
        break;

    case DISCHARGE:
        printf("Stato: scarico concime\n");
        break;

    case CHARGE:
        printf("Stato: carico concime\n");
        break;
    
    default:
        printf("Stato: sconosciuto");
        break;
    }
}

void print_infos(void *pvParameter) {
    while(1) {
        printf("Cassetto sinistro:\n");
        print_drawer(drawer_sx);
        printf("\n-----------------------------\n");

        printf("Cassetto destro:\n");
        print_drawer(drawer_dx);
        printf("\n-----------------------------\n");

        printf("tg_speed_val = %lf km/h\n", tg_speed_val);
        printf("thg_speed_val = %lf km/h\n", thg_speed_val);
        printf("pto_pos_val = %lf rps/h\n", pto_pos_val);
        if(pto_work)
            printf("pto_work = true\n");
        else
            printf("pto_work = false\n");
        printf("\n------------------------------\n");

        vTaskDelay(1000 / portTICK_PERIOD_MS);
    }
}

void app_main(void)
{
    var_init();
    io_init();

    xTaskCreatePinnedToCore(drawer_inputs_handler, "gpio_sx", 1024, (void*) &drawer_sx_in, 5, NULL, 0);
    xTaskCreatePinnedToCore(drawer_inputs_handler, "gpio_dx", 1024, (void*) &drawer_dx_in, 5, NULL, 0);
    xTaskCreatePinnedToCore(drawer_output_handler, "drawer_sx", 1024, (void*) &drawer_sx, 5, NULL, 0);
    xTaskCreatePinnedToCore(drawer_output_handler, "drawer_dx", 1024, (void*) &drawer_dx, 5, NULL, 0);

    xTaskCreatePinnedToCore(tractor_input_handler, "tractor_in", 2048, NULL, 5, NULL, 1);
    xTaskCreatePinnedToCore(print_infos, "printer", 2048, NULL, 5, NULL, 1);
    xTaskCreatePinnedToCore(manage_screens, "screens", 8192, NULL, 5, NULL, 1);

    //for( ;; );
}

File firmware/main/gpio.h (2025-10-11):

#include "driver/gpio.h"

#define RELAY1_GPIO 21
#define RELAY2_GPIO 47
#define RELAY3_GPIO 48
#define RELAY4_GPIO 37

#define INTSX_GPIO 4
#define INTDX_GPIO 5

#define PULSX_GPIO 6
#define PULDX_GPIO 7

#define SDA_GPIO 15
#define SCL_GPIO 16

#define FOTSX_GPIO 10
#define FOTDX_GPIO 11

#define MAGNETSX_GPIO 12
#define MAGNETDX_GPIO 13

#define PTO_POS_GPIO 38
#define PTO_WORK_GPIO 9

#define TG_SPEED_GPIO 36
#define THG_SPEED_GPIO 35

typedef struct {
    gpio_num_t sda;
    gpio_num_t scl;
}i2c_pins_t;

typedef struct {
    gpio_num_t drawer_up;
    gpio_num_t drawer_down;
}drawer_out;

typedef struct {
    gpio_num_t photocell;
    gpio_num_t int_fot;
    gpio_num_t puls;
    gpio_num_t mag_sens;

    bool start_state;
    bool tail;
    bool read_mag_sens;
}drawer_in;

static i2c_pins_t i2c0 = {
    .sda = SDA_GPIO,
    .scl = SCL_GPIO
};

static drawer_out drawer_sx_out = {
    .drawer_down = RELAY1_GPIO,
    .drawer_up = RELAY2_GPIO
};

static drawer_out drawer_dx_out = {
    .drawer_down = RELAY3_GPIO,
    .drawer_up = RELAY4_GPIO
};

static drawer_in drawer_sx_in = {
    .photocell = FOTSX_GPIO,
    .int_fot = INTSX_GPIO,
    .puls = PULSX_GPIO,
    .mag_sens = MAGNETSX_GPIO
};

static drawer_in drawer_dx_in = {
    .photocell = FOTDX_GPIO,
    .int_fot = INTDX_GPIO,
    .puls = PULDX_GPIO,
    .mag_sens = MAGNETDX_GPIO
};

void print_drawer_input(drawer_in input);
void print_drawer_output(drawer_out output);

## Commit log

2025-12-06 pcbs update
    [DinoSpand_v2.0-B_Cu.gbr, DinoSpand_v2.0-B_Mask.gbr, DinoSpand_v2.0-B_Paste.gbr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]
2025-12-27 pcbs final update
    [DinoSpand_v2.0.kicad_pcb, microcontroller.kicad_sch]
2026-02-27 Enhance README with PCBWay production details
    Added a section about PCBWay production experience and firmware.
2026-03-03 Link to PCBWay
